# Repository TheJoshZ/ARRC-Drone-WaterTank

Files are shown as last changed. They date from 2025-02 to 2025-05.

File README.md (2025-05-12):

# ARRC-Drone-WaterTank

## 1.0 Introduction  
This is my contribution to UBCO's participation in the 2025 AEAC National Student UAS Competition. In essence, part 2 of the competition outlines that the team must transport water to various hotspots using a drone. To achieve this, the team has decided to use a water tank, the design of which was completed by me and a few others. I will walk you through the design process I took, as well as each iteration of the water tank's design.  

## V0  

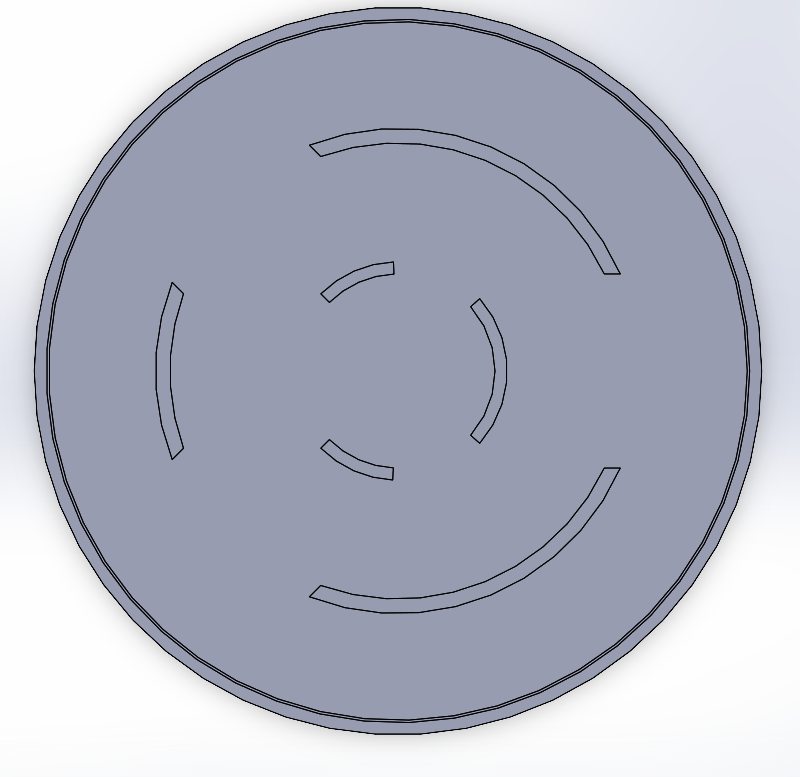
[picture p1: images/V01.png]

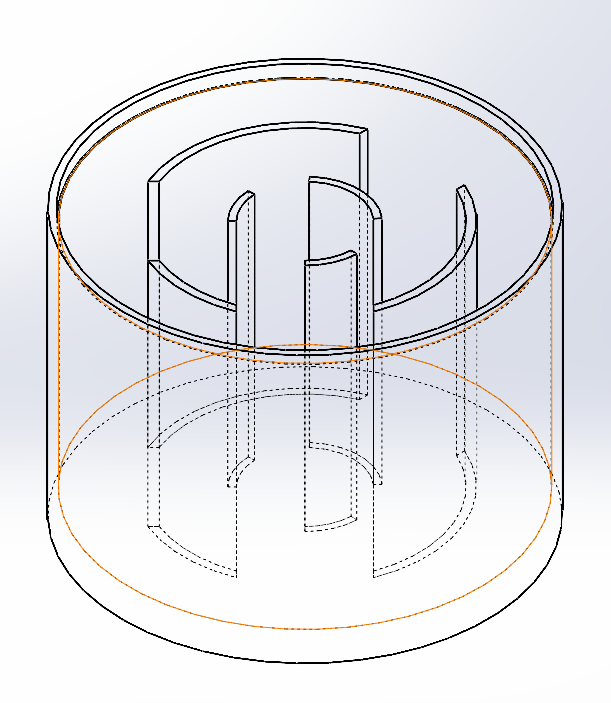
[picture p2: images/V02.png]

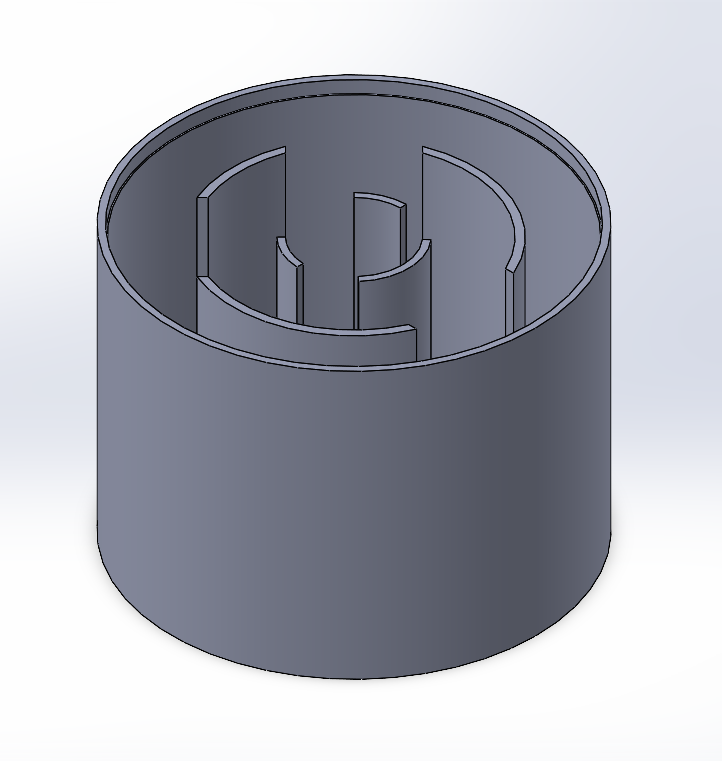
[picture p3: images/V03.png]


The main thing to note with version 0 is the design of the baffles. Our primary concern was the sloshing caused by the water within the tank. Since this tank was placed a considerable distance from the center of mass of the drone, and we were considering carrying up to 4L of water, the focus was placed on designing baffles. Our goal was to minimize the headache experienced by the software team by reducing/eliminating oscillations caused by water movement within the tank.  

As you can see, I went with a **circular baffle design**, while the rest of my peers went with a simpler square grid baffle. During the meeting of the water tank team, my design was chosen because **when the drone rotates, which it does often, square baffles mean that it will have to carry the inertia of the water with it while it rotates, whereas circular/axially symmetric baffles eliminate that inertia while still segregating the water**.  

## V1  
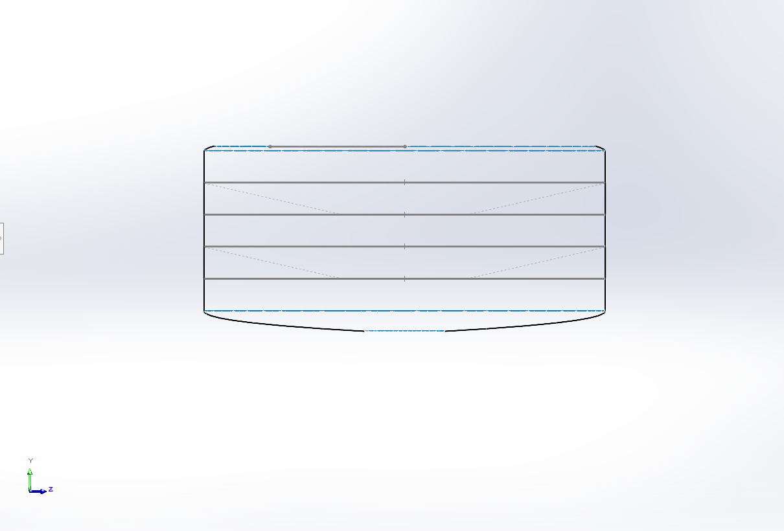
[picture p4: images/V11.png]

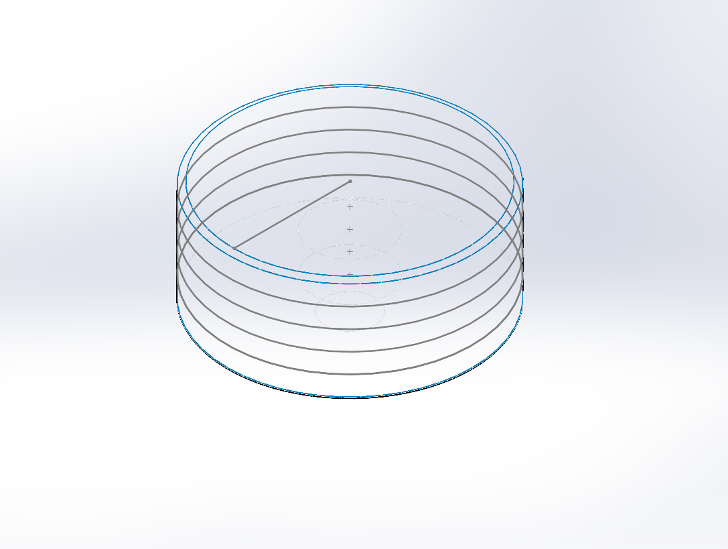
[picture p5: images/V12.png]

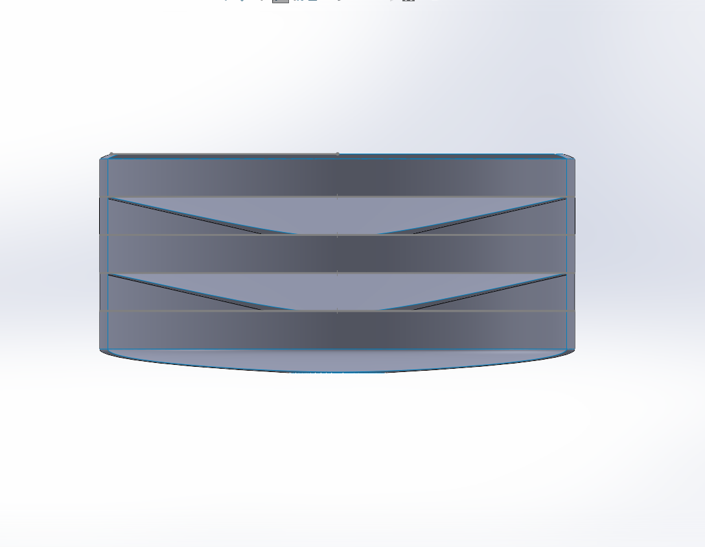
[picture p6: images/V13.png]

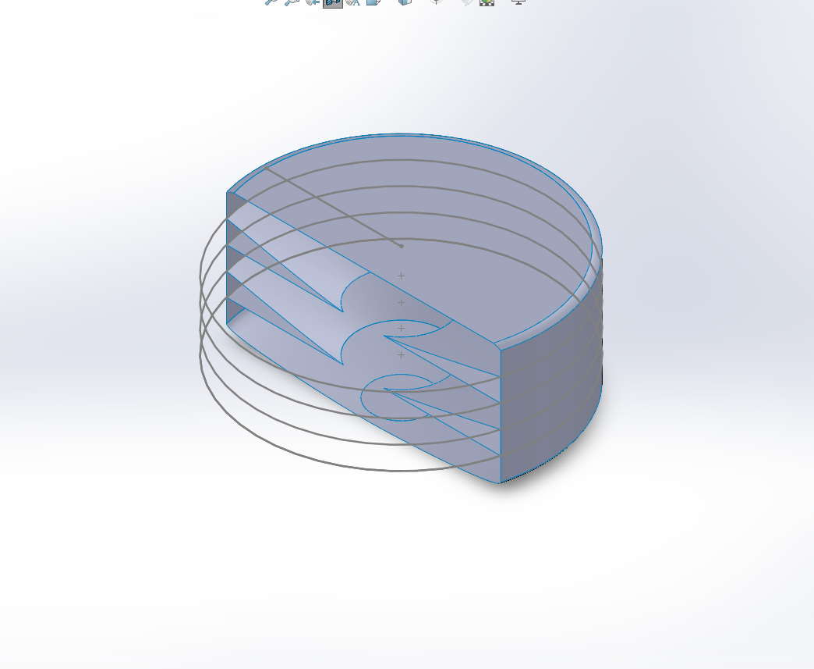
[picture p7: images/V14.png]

The baffle has been completely redesigned in this version. My proposal for the new baffle design is the one currently being used on the drone. Instead of using vertical baffles to distribute the momentum of the water hitting the side of the tank, I used **horizontal baffles to eliminate any sloshing at all**.  

We have chosen to deposit 500ml of water to each hotspot, hence a horizontal baffle was placed every 500ml within the tank. The angle of the baffle is based on the maximum amount of tilt the drone will experience during flight, as this would seal off the free surface when the drone tilts. Feel free to ask me more about this during the interview! I would love to expand on this more!  

Since we still planned to carry 4L of water, we would need 8 compartments, meaning 7 horizontal baffles would be needed. As you can see, only 2 are shown in the picture. This is due to an error in volume calculation, which will be addressed in future versions.  

## V2 to V3  
Mostly changing the dimensions due to physical constraints of the drone. However, the general design for the tank and the baffles remains the same. V3 saw the volume shrink to 2.5L due to the max weight constraint of 15kg and motor/battery upgrades made on the drone.  

## V4 
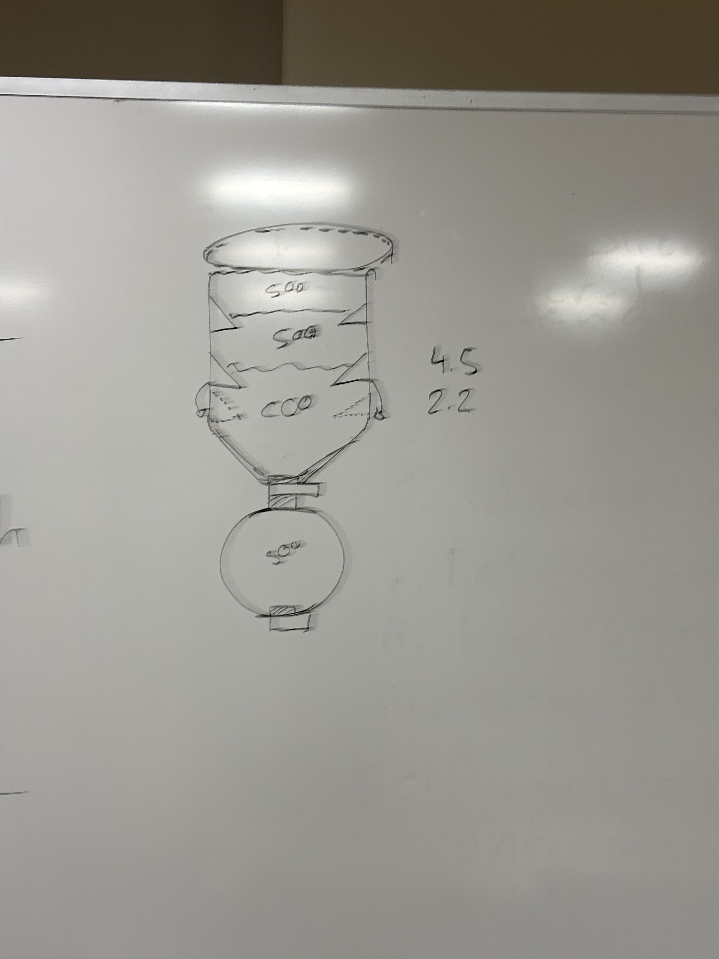
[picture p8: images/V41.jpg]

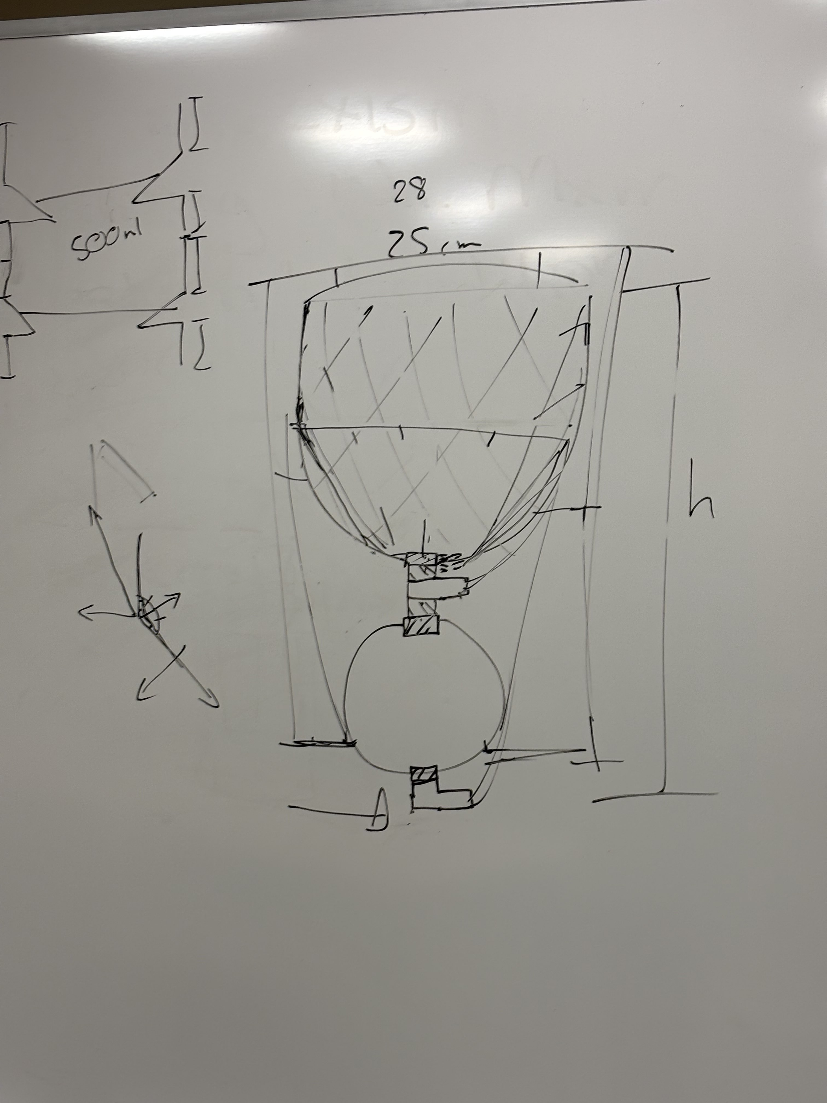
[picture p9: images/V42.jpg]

A major redesign of the tank for the drone. Instead of having one large tank, we now have a primary and secondary tank. This serves two purposes.  

Firstly, as we need to deposit precisely 500ml of water at each hotspot, having a secondary tank connected to the primary tank makes manufacturing much easier. It is easier to manufacture an entire tank to 500ml than to manufacture the bottom volume (the 500ml volume created using baffles in the 2.5L tank) of a singular tank to 500ml.  

Secondly, this solves the issue of needing to embed an electronic valve inside the tank, as two valves were needed in the original design—one at the exit and one at the first baffle from the bottom up inside the tank. I would also love to clarify why we need two valves if it is not clear!  

Therefore, this is the design we decided on: a secondary tank with a volume of 500ml and a primary tank with a volume of 1.7L (1.5L + 0.5L overhead).  

## 2.0 Final Product

Water Tank mounted to the drone

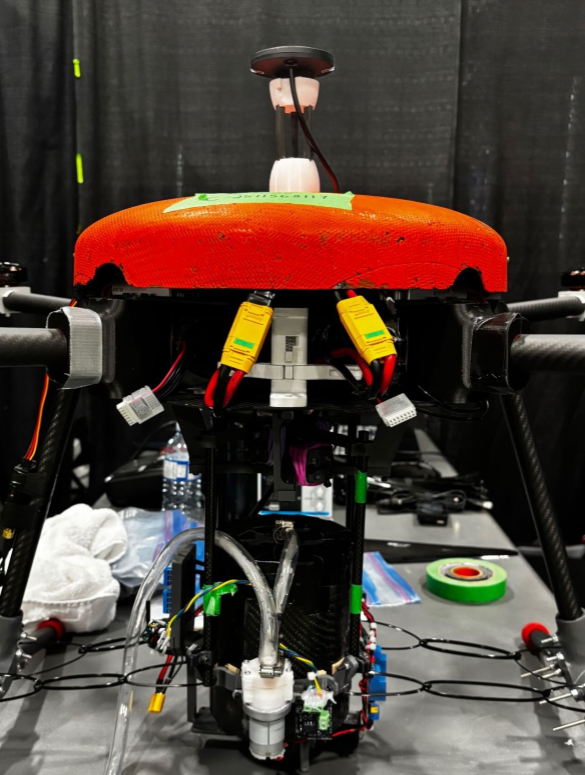
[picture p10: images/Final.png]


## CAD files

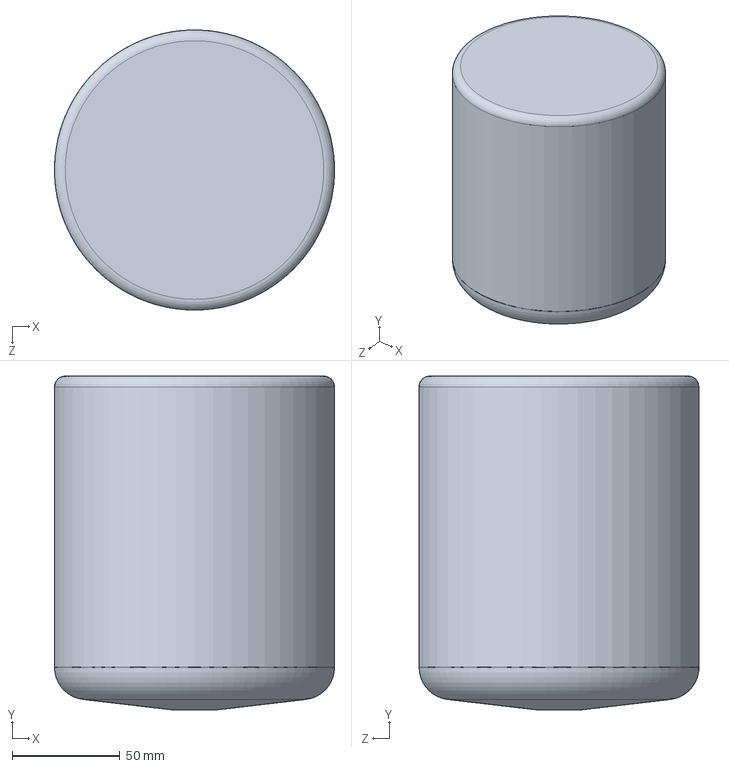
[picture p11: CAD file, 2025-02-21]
Tank V4 main.SLDPRT
130.0 x 155.0 x 130.0 mm

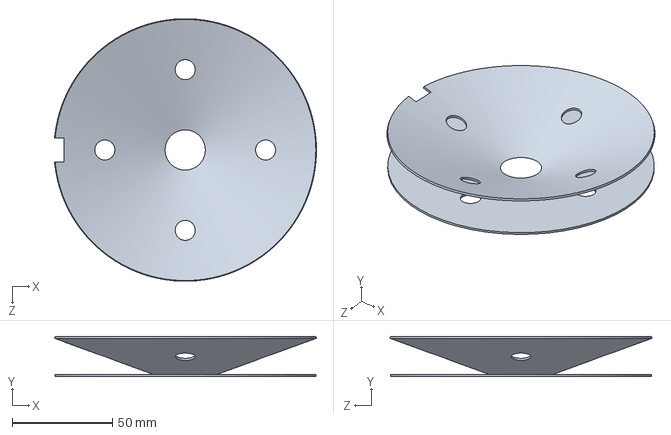
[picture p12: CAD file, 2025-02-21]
V4 Baffle 20Deg.SLDPRT
130.4 x 20.0 x 130.6 mm

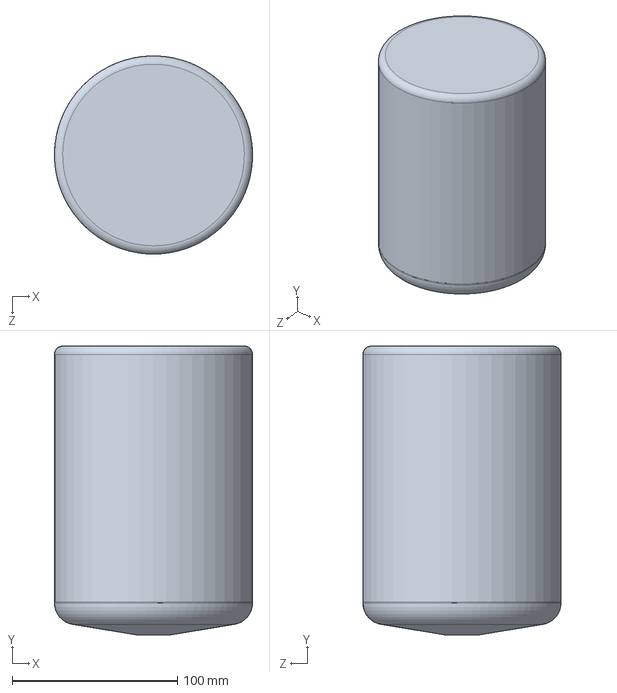
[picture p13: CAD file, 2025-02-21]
Tank V3.SLDPRT
120.0 x 175.0 x 120.0 mm

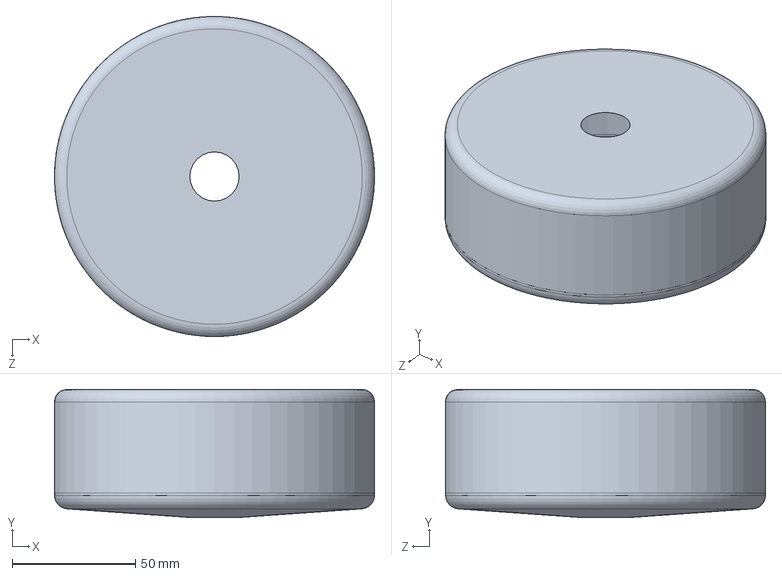
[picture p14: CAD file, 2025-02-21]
Tank V4 secondary.SLDPRT
130.0 x 52.0 x 130.0 mm

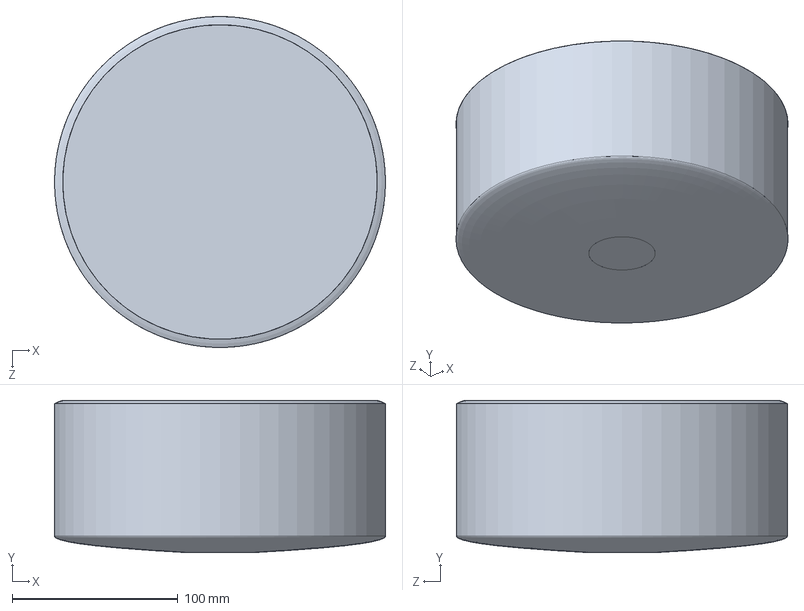
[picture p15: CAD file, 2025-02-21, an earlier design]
Tank V1.SLDPRT
200.0 x 92.0 x 200.0 mm

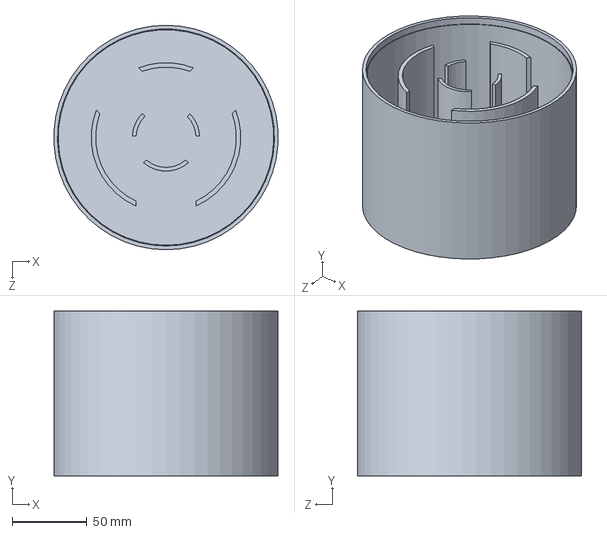
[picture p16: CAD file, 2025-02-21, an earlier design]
Tank V0.SLDPRT
149.7 x 110.0 x 150.0 mm

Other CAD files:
Tank V2.SLDPRT
